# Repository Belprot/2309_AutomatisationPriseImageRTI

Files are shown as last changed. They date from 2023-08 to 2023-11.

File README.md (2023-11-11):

# 2309_AutomatisationPriseImageRTI - Diploma project

## [Projet report](doc/2309_AutomatisationPriseImagesRTI_Rapport_v1_0_0.pdf)

## Project poster
1696541977120-d4f3472b-acff-401a-b088-3b05499086cd_1

## 3D PCB pictures
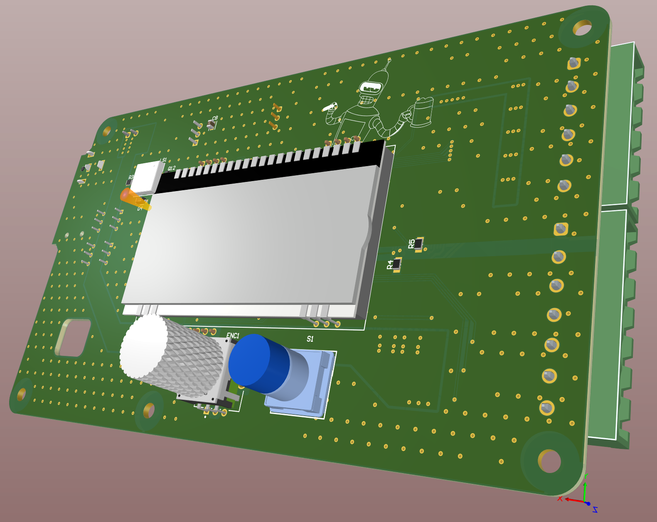
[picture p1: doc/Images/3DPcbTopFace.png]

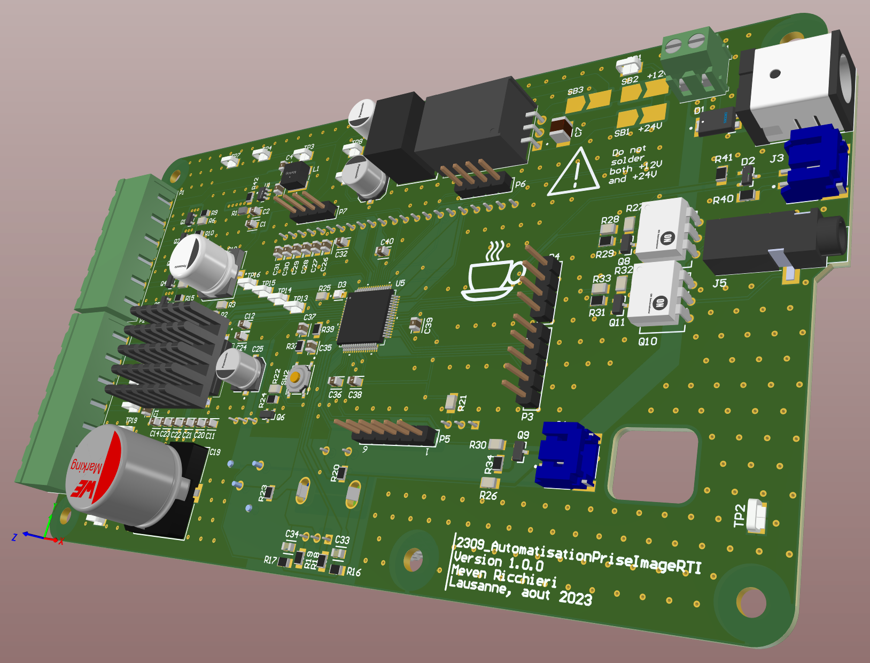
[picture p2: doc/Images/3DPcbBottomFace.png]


## 3D Integration
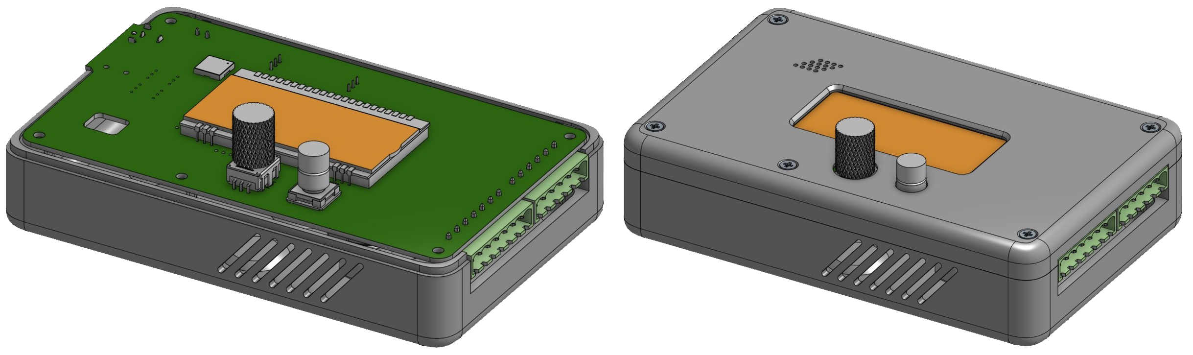
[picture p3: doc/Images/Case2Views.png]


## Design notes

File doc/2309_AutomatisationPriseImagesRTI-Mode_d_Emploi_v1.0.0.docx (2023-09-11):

2309_AutomatisationPriseImagesRTI-Mode_d_Emlpoi_v1.0.0

Mode d’emploi du système :

Le fonctionnement du système est intuitif et facile à maîtriser. Le menu principal propose deux modes d'opération : le mode capture et le mode réglage. Un troisième menu permet de consulter les informations du système sans possibilité d'interaction.

Dans le mode capture, vous pouvez prendre des images de l'objet préalablement placé au centre de la machine. Vous avez le choix entre deux modes de capture : manuel et automatique.

Le mode manuel vous donne un contrôle total sur l'angle du bras motorisé équipé des LEDs de puissance. Vous pouvez également choisir quand déclencher une séquence de prise de 5 images. Dans ce mode, vous avez la possibilité d'indexer la machine pour obtenir l'angle 0 à l'emplacement de l'index. Pour ajuster l'angle du bras, activez la modification de position et tournez l'encodeur. Pour lancer la séquence, appuyez simplement une fois sur le bouton poussoir.

Le mode automatique vous permet de lancer une séquence complète de prise d'images, généralement environ 200 photos de l'objet.

Le menu des réglages vous permet de personnaliser le comportement de la machine pour qu'elle réponde à vos besoins spécifiques. Il est crucial de noter que certaines configurations incorrectes, notamment celles liées au moteur, peuvent rendre le système inutilisable. Une fois que vous avez effectué vos réglages, vous avez la possibilité de sauvegarder la configuration pour qu'elle soit conservée en mémoire et chargée automatiquement au démarrage de la machine.

La Figure ci-dessous présente une vue d'ensemble de tous les menus disponibles.

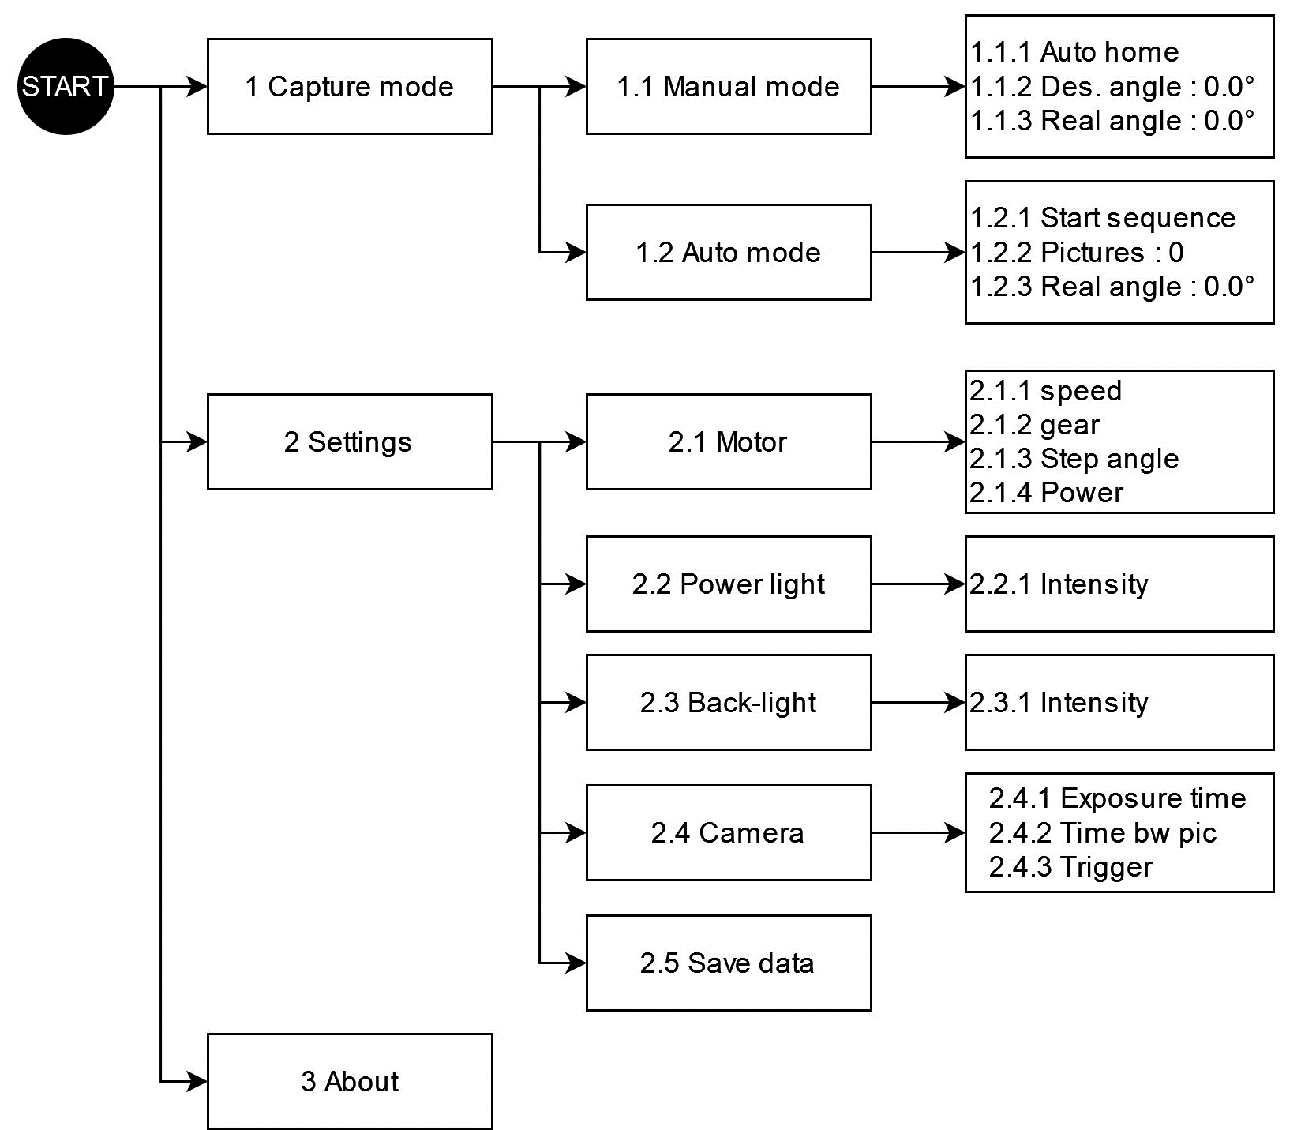
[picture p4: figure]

Figure 1 – Menus

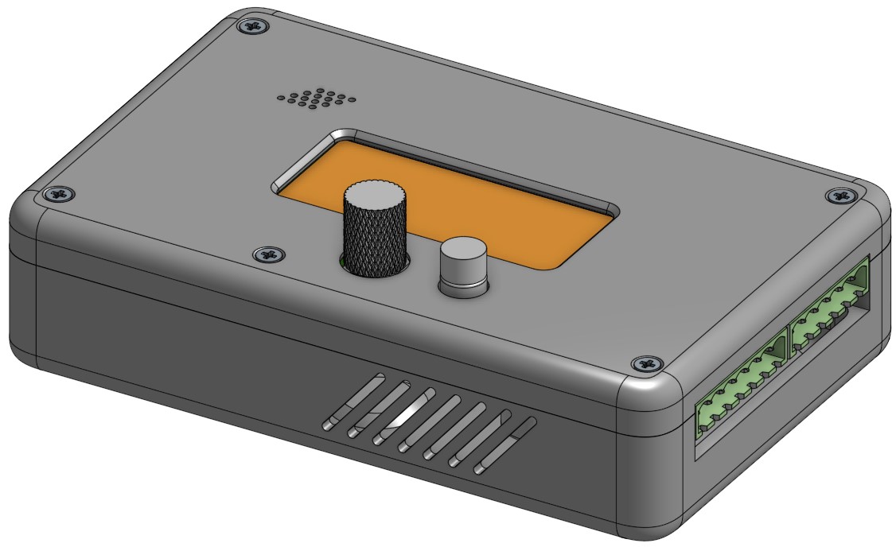
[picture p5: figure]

Connecteur LEDs

Encodeur rotatif

Bouton poussoir

Connecteur moteur

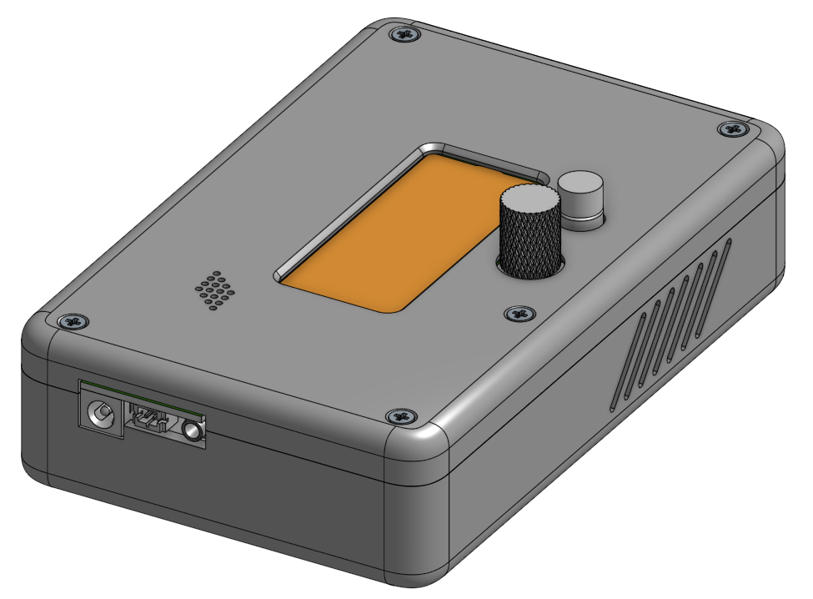
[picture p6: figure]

Connecteur appareil photo

Connecteur contact Reed d’indexage

Connecteur d’alimentation 24V

Meven Ricchieri

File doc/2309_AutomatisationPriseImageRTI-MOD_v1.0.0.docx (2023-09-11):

# Projet ETML-ES – Modification

PROJET: | 2309_AutomatisationPriseImageRTI_v1.0.0
Entreprise/Client: | MCAH / M. Mathieu Bernard-Reymond | Département: | SLO
Demandé par (Prénom, Nom): | M. Serge Castoldi | Date: | 11.09.2023
Objet (No ou réf, pièce, PCB...) | 2309
Version à modifier: | V1

Auteur (ETML-ES): | | Filière: | SLO
Nouvelle version: | | Date:

# 1 Description ou justification

La modifications 1 va permettre d’obtenir un filtre passe bas fonctionnel permettant de limiter le nombre de rebonds du PEC12.

# 2 Référence conception

K:\ES\PROJETS\SLO\2309_AutomatisationPriseImageRTI

# 3 Détail des modifications

# | Description | Fait | Approuvé

1 | Modifier le schéma du filtre du PEC12, R16 doit être connecté directement à la sortie du CHANNEL A et R17 doit être connecté directement à la sortie du CHANNEL B. | NOK
2 | Rechercher l’origine du courant réduit du driver de LED puis effectuer la modification. Piste : Tension d’alimentation trop basse, tester avec alimentation 24V | NOK
3
4
5
6

# 4 Remarques

JMO – Nov 20182309_AutomatisationPriseImageRTI-MOD_v1.0.0.docxPage 1

ECOLE SUPERIEURE ELCO – SLO

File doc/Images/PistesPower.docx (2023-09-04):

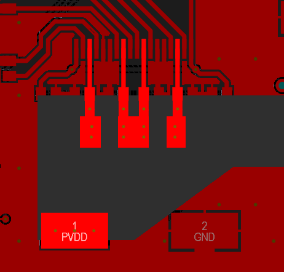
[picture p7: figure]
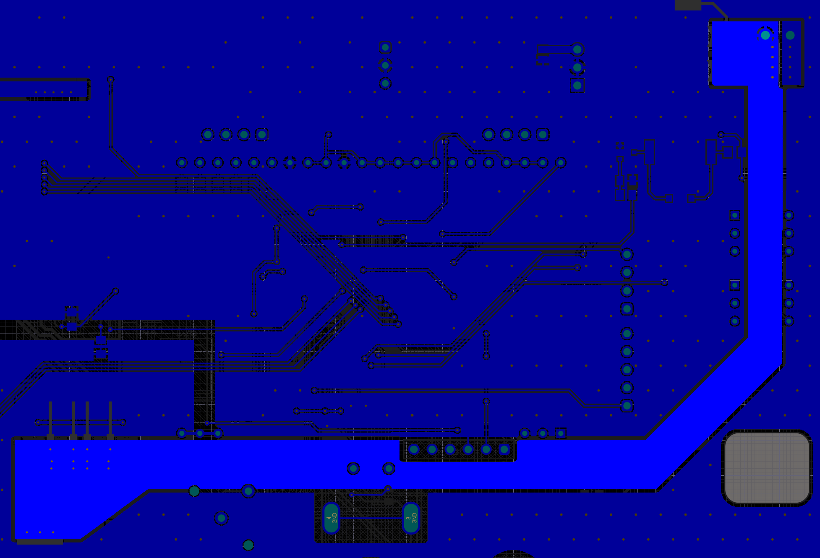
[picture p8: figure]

Entrée d’alimentation du driver en top layer

Driver moteur DRV8432DKD

Entrée de puissance (+24V)

Vue bottom

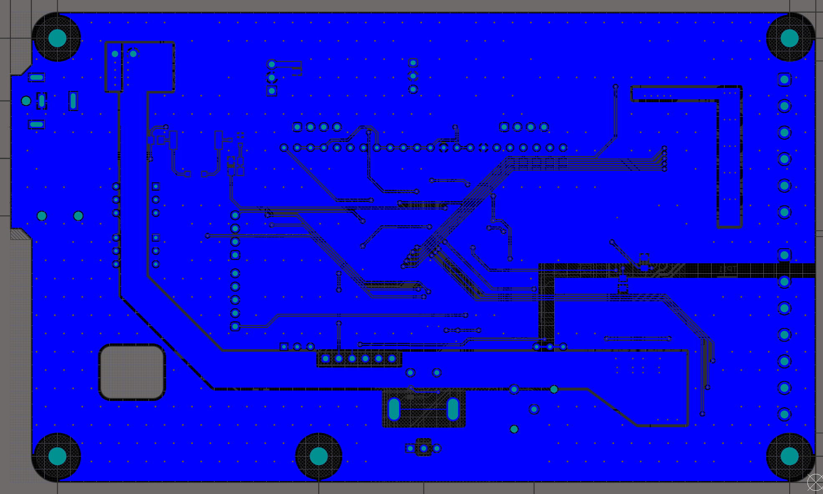
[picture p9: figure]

Retour courant 12V driver LED

Retour courant 24V (moteur)

Retour courant 3.3V

Driver moteur (top layer)

GND

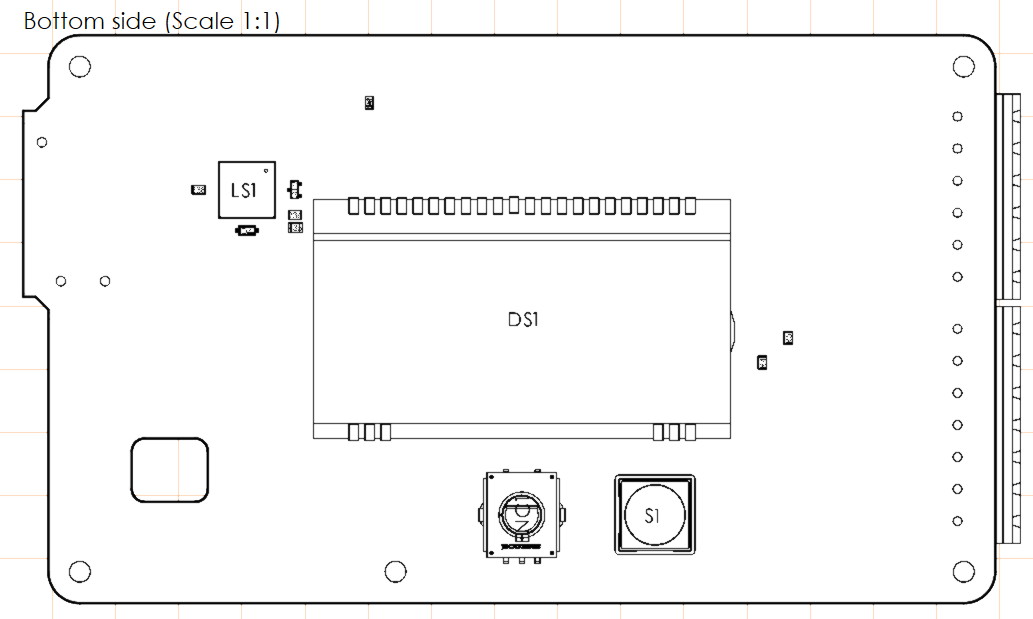
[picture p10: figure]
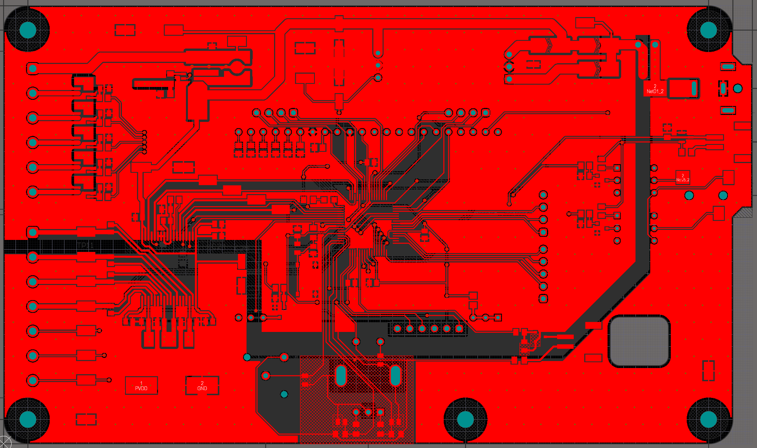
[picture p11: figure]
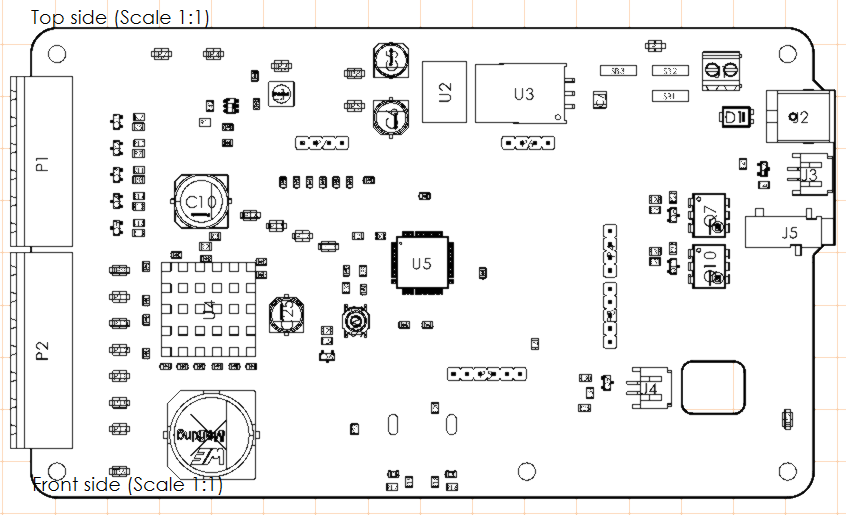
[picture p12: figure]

Connecteur de programmation

Optocoupleurs

MOSFETs de multiplexage

Driver LED

Driver moteur

MCU

Sortie régulateur 12V

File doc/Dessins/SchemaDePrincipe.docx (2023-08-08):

Electronique de commande

Bras motorisé

LEDs de puissance

Élément à photographier

Armature

Moteur de positionnement

Appareil photo

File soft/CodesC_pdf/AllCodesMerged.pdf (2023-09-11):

1 /*******************************************************************************

### 2 MPLAB Harmony Application Source File

3

### 4 Company:

5 Microchip Technology Inc.
6

### 7 File Name: 8 app.c

9

### 10 Summary:

11 This file contains the source code for the MPLAB Harmony application. 12

### 13 Description: 14 This file contains the source code for the MPLAB Harmony application. It 15 implements the logic of the application's state machine and it may call

16 API routines of other MPLAB Harmony modules in the system, such as drivers,

17 system services, and middleware. However, it does not call any of the 18 system interfaces (such as the "Initialize" and "Tasks" functions) of any of 19 the modules in the system or make any assumptions about when those functions 20 are called. That is the responsibility of the configuration-specific system

21 files.
22 *******************************************************************************/ 23
24 // DOM-IGNORE-BEGIN
25 /******************************************************************************* 26 Copyright (c) 2013-2014 released Microchip Technology Inc. All rights reserved. 27

### 28 Microchip licenses to you the right to use, modify, copy and distribute 29 Software only when embedded on a Microchip microcontroller or digital signal 30 controller that is integrated into your product or third party product

31 (pursuant to the sublicense terms in the accompanying license agreement). 32

### 33 You should refer to the license agreement accompanying this Software for

34 additional information regarding your rights and obligations.
35
36 SOFTWARE AND DOCUMENTATION ARE PROVIDED "AS IS" WITHOUT WARRANTY OF ANY KIND,

### 37 EITHER EXPRESS OR IMPLIED, INCLUDING WITHOUT LIMITATION, ANY WARRANTY OF

38 MERCHANTABILITY, TITLE, NON-INFRINGEMENT AND FITNESS FOR A PARTICULAR PURPOSE.

39 IN NO EVENT SHALL MICROCHIP OR ITS LICENSORS BE LIABLE OR OBLIGATED UNDER 40 CONTRACT, NEGLIGENCE, STRICT LIABILITY, CONTRIBUTION, BREACH OF WARRANTY, OR 41 OTHER LEGAL EQUITABLE THEORY ANY DIRECT OR INDIRECT DAMAGES OR EXPENSES 42 INCLUDING BUT NOT LIMITED TO ANY INCIDENTAL, SPECIAL, INDIRECT, PUNITIVE OR 43 CONSEQUENTIAL DAMAGES, LOST PROFITS OR LOST DATA, COST OF PROCUREMENT OF 44 SUBSTITUTE GOODS, TECHNOLOGY, SERVICES, OR ANY CLAIMS BY THIRD PARTIES

45 (INCLUDING BUT NOT LIMITED TO ANY DEFENSE THEREOF), OR OTHER SIMILAR COSTS.
46 *******************************************************************************/ 47 // DOM-IGNORE-END
48
49
50 // ***************************************************************************** 51 // ***************************************************************************** 52 // Section: Included Files
53 // ***************************************************************************** 54 // ***************************************************************************** 55
56 #include "app.h"
57 #include "Mc32_spi_sm.h"
58 #include "lcd_spi.h"
59 #include "system/devcon/src/sys_devcon_local.h" 60 #include "pec12.h"
61 #include "menu.h"
62
63
64
65 // ***************************************************************************** 66 // ***************************************************************************** 67 // Section: Global Data Definitions
68 // ***************************************************************************** 69 // *****************************************************************************

70
71 // ***************************************************************************** 72 /* Application Data
73

### 74 Summary: 75 Holds application data

76

### 77 Description:

78 This structure holds the application's data.
79

### 80 Remarks:

81 This structure should be initialized by the APP_Initialize function. 82
83 Application strings and buffers are be defined outside this structure. 84 */
85
86 APP_DATA appData;
87 SW S1;
88
89 // ***************************************************************************** 90 // ***************************************************************************** 91 // Section: Application Callback Functions
92 // ***************************************************************************** 93 // ***************************************************************************** 94
95 /* TODO: Add any necessary callback functions.
96 */
97
98 // ***************************************************************************** 99 // ***************************************************************************** 100 // Section: Application Local Functions
101 // ***************************************************************************** 102 // ***************************************************************************** 103
104
105 /* TODO: Add any necessary local functions.
106 */
107
108
109 // ***************************************************************************** 110 // ***************************************************************************** 111 // Section: Application Initialization and State Machine Functions
112 // ***************************************************************************** 113 // ***************************************************************************** 114
115
116 //----------------------------------------------------------------------------// APP_UpdateAppState
117 void APP_UpdateAppState(APP_STATES newState){
118
119 appData.appState = newState;
120 }
121
122 //----------------------------------------------------------------------------// APP_Initialize
123 void APP_Initialize ( void )
124 {
125 SPI_Init();
126 /* Place the App state machine in its initial state. */ 127 appData.appState = APP_STATE_INIT;
128 appData.msCounter = 0;
129 appData.backLightIntensitiy = 2500; /* 100% */
130 appData.lightIntensity = 2500; /* 100% */ 131 appData.exposureDuration = 100;
132 appData.timeBetweenPictures = 1000;
133 appData.isFiveShotsSeqEnable = false; 134 appData.seqClock1_ms = 0;
135 appData.angleBwEachSeq = 10;
136 appData.nbrOfShotsPerformed = 0;

137 appData.buzzerIntensity = 2500; 138 appData.valSeq = 0;
139
140 initMenuParam();
141 initStepperParam();
142 }
143
144
145
146 //----------------------------------------------------------------------------// APP_Tasks
147 void APP_Tasks ( void ){
148
149 static uint16_t counter1 = 0; 150 static uint16_t counter2 = 0; 151
152 /* Main state machine */
153 switch(appData.appState){
154 //--------------------------------------------------------------------// APP_STATE_INIT
155 case APP_STATE_INIT:
156 /* Read data from EEPROM to restore presets */
157 readDataFromEeprom(getMyStepperStruct());
158 /* Initialization of the motor */
159 initStepperMotor();
160 /* Update MCPWM Duty-cycle of other PWM with EEPROM data */ 161 updateMcpwmDuty();
162 /* Turn on MCPWM */
163 PLIB_MCPWM_Enable(MCPWM_ID_0);
164 /* Initialization sequence */ 165 initLcd();
166 /* Print initialization menu */ 167 printLcdInit();
168 /* Start useful Timers */
169 DRV_TMR1_Start();
170 DRV_TMR2_Start();
171 /* Print main menu once all peripherals are configured */ 172 printMainMenu();
173 /* States machines update */
174 APP_UpdateAppState(APP_STATE_WAIT);
175 break;
176
177 //--------------------------------------------------------------------// APP_STATE_SERVICE_TASKS
178 /* Frequency = 10'000Hz */
179 case APP_STATE_SERVICE_TASKS:
180
181 /* Process who is responsible of the sequence, motor orders and 182 * lights orders. */
183
184 | // | SIGN_LED_CMDToggle();
185 sequenceManagementProcess(); 186
187 if(counter2 >= 10){
188 /* Frequency = 1'000Hz */
189 counter2 = 0;
190 /* Scan the activity of the rotary encoder */ 191 scanPec12();
192 /* Scan the activity of the switch S1 */ 193 scanSwitch();
194 }
195 if(counter1 >= 1000){
196 /* Frequency = 10Hz */ 197 counter1 = 0;
198 menuManagementProcess(); 199 }
200 counter1++;
201 counter2++;
202

203
204 // Calls the SPI do task state machine 205 SPI_DoTasks();
206
207 /* States machines update */
208 APP_UpdateAppState(APP_STATE_WAIT);
209 break;
210 //--------------------------------------------------------------------// APP_STATE_WAIT
211 case APP_STATE_WAIT:
212 /* Nothing is supposed to happen here */
213 break;
214
215 //--------------------------------------------------------------------// default 216 default:
217 break;
218 }
219 }
220
221
222 //----------------------------------------------------------------------------// APP_Delay_ms
223 void APP_Delay_ms(uint32_t ms){
224
225 DRV_TMR3_Start();
226 | // | SIGN_LED_CMDToggle();
227 while(appData.msCounter < ms){ 228
229 }
230 | // | SIGN_LED_CMDToggle();
231
232 DRV_TMR3_Stop();
233 appData.msCounter = 0;
234 }
235
236 //----------------------------------------------------------------------------// setBlIntensity
237 void setBlIntensity(int32_t *backLightIntensitiy){
238
239 // Limit values to avoid problems
240 if(*backLightIntensitiy < BACKLIGHT_INTENSITY_MIN) *backLightIntensitiy 241 = BACKLIGHT_INTENSITY_MIN;
242 if(*backLightIntensitiy > BACKLIGHT_INTENSITY_MAX) *backLightIntensitiy 243 = BACKLIGHT_INTENSITY_MAX;
244
245 /* 25 = 2500 / 100 */
246 appData.backLightIntensitiy = *backLightIntensitiy * 25; 247 PLIB_MCPWM_ChannelPrimaryDutyCycleSet(MCPWM_ID_0, PWM_BL_CH, 248 appData.backLightIntensitiy);
249 }
250 int32_t getBlIntensity(void){
251
252 return appData.backLightIntensitiy / 25; 253 }
254
255
256 //----------------------------------------------------------------------------// scanSwitch
257 void scanSwitch(void){
258
259 // Save old states for debounce 260 S1.state[3] = S1.state[2]; 261 S1.state[2] = S1.state[1]; 262 S1.state[1] = S1.state[0]; 263 S1.state[0] = SWITCHStateGet();
264
265 // Check if switch is pressed
266 if(S1.state[0] == 1 && S1.state[1] == 1
267 && S1.state[2] == 0 && S1.state[3] == 0){

268
269 S1.isPressed = true;
270 }
271 }
272 //----------------------------------------------------------------------------// getSwitchEvent
273 bool getSwitchEvent(void){
274
275 bool isPressed = S1.isPressed; 276 S1.isPressed = 0;
277
278 return isPressed;
279 }
280
281 //----------------------------------------------------------------------------// initLcdSeq
282 void initLcd(void){
283
284 RESET_LCD_CMDOff();
285 APP_Delay_ms(1);
286 RESET_LCD_CMDOn();
287 APP_Delay_ms(10);
288 initDispl();
289 /* Create degree symbol for LCD uses */ 290 CreateLcdDegreeSymbol(0x01);
291 }
292
293 void updateMcpwmDuty(void){
294
295 /* Update PWMs DutyCycle with data from EEPROM */
296 PLIB_MCPWM_ChannelPrimaryDutyCycleSet(MCPWM_ID_0, PWM_BL_CH, 297 appData.backLightIntensitiy);
298 PLIB_MCPWM_ChannelPrimaryDutyCycleSet(MCPWM_ID_0, PWM_BUZZER_CH, 299 appData.buzzerIntensity);
300 PLIB_MCPWM_ChannelPrimaryDutyCycleSet(MCPWM_ID_0, PWM_DIM_CH, 301 appData.lightIntensity);
302 }
303
304
305
306
307
308 /******************************************************************************* 309 End of File
310 */
311

1 /******************************************************************************* 2 MPLAB Harmony Application Header File
3
4 Company:
5 Microchip Technology Inc.
6
7 File Name:
8 app.h
9
10 Summary:
11 This header file provides prototypes and definitions for the application. 12
13 Description:
14 This header file provides function prototypes and data type definitions for 15 the application. Some of these are required by the system (such as the 16 "APP_Initialize" and "APP_Tasks" prototypes) and some of them are only used 17 internally by the application (such as the "APP_STATES" definition). Both 18 are defined here for convenience.
19 *******************************************************************************/ 20
21 //DOM-IGNORE-BEGIN
22 /******************************************************************************* 23 Copyright (c) 2013-2014 released Microchip Technology Inc. All rights reserved. 24
25 Microchip licenses to you the right to use, modify, copy and distribute
26 Software only when embedded on a Microchip microcontroller or digital signal 27 controller that is integrated into your product or third party product
28 (pursuant to the sublicense terms in the accompanying license agreement). 29
30 You should refer to the license agreement accompanying this Software for
31 additional information regarding your rights and obligations.
32
33 SOFTWARE AND DOCUMENTATION ARE PROVIDED "AS IS" WITHOUT WARRANTY OF ANY KIND, 34 EITHER EXPRESS OR IMPLIED, INCLUDING WITHOUT LIMITATION, ANY WARRANTY OF
35 MERCHANTABILITY, TITLE, NON-INFRINGEMENT AND FITNESS FOR A PARTICULAR PURPOSE. 36 IN NO EVENT SHALL MICROCHIP OR ITS LICENSORS BE LIABLE OR OBLIGATED UNDER
37 CONTRACT, NEGLIGENCE, STRICT LIABILITY, CONTRIBUTION, BREACH OF WARRANTY, OR 38 OTHER LEGAL EQUITABLE THEORY ANY DIRECT OR INDIRECT DAMAGES OR EXPENSES
39 INCLUDING BUT NOT LIMITED TO ANY INCIDENTAL, SPECIAL, INDIRECT, PUNITIVE OR 40 CONSEQUENTIAL DAMAGES, LOST PROFITS OR LOST DATA, COST OF PROCUREMENT OF
41 SUBSTITUTE GOODS, TECHNOLOGY, SERVICES, OR ANY CLAIMS BY THIRD PARTIES
42 (INCLUDING BUT NOT LIMITED TO ANY DEFENSE THEREOF), OR OTHER SIMILAR COSTS.
43 *******************************************************************************/ 44 //DOM-IGNORE-END
45
46 #ifndef _APP_H
47 #define _APP_H
48
49 // ***************************************************************************** 50 // ***************************************************************************** 51 // Section: Included Files
52 // ***************************************************************************** 53 // ***************************************************************************** 54
55 #include "stepperDriver.h"
56 #include "lights.h"
57 #include <stdint.h>
58 #include <stdbool.h>
59 #include <stddef.h>
60 #include <stdlib.h>
61 #include <stdio.h>
62 #include "system_config.h"
63 #include "system_definitions.h"
64
65 // DOM-IGNORE-BEGIN
66 #ifdef __cplusplus // Provide C++ Compatibility 67
68 extern "C" {
69

70 #endif
71 // DOM-IGNORE-END
72
73 // ***************************************************************************** 74 // ***************************************************************************** 75 // Section: Type Definitions
76 // ***************************************************************************** 77 // ***************************************************************************** 78
79 #define SYS_CLK 40000000
80
81 #define PWM_A_CMD_CH MCPWM_CHANNEL1 82 #define PWM_B_CMD_CH MCPWM_CHANNEL1 83 #define PWM_C_CMD_CH MCPWM_CHANNEL2 84 #define PWM_D_CMD_CH MCPWM_CHANNEL2 85 #define PWM_BL_CH MCPWM_CHANNEL3 86 #define PWM_BUZZER_CH MCPWM_CHANNEL4 87 #define PWM_DIM_CH MCPWM_CHANNEL6 88
89 #define MARGIN_LED_DELAY 50
90
91 /* Intensity in percent */
92 #define BACKLIGHT_INTENSITY_MIN 0 93 #define BACKLIGHT_INTENSITY_MAX 100
94
95
96 /* Value used to check if the EEPROM is already writent by this code */
97 #define CONTROL_VALUE 0x11223344
98
99 // ***************************************************************************** 100 /* Application states
101
102 Summary:
103 Application states enumeration
104
105 Description:
106 This enumeration defines the valid application states. These states 107 determine the behavior of the application at various times.
108 */
109
110 typedef enum
111 {
112 /* Application's state machine's initial state. */ 113 APP_STATE_INIT=0,
114 APP_STATE_SERVICE_TASKS,
115 APP_STATE_SERVICE_CAPTURE,
116 APP_STATE_WAIT,
117 } APP_STATES;
118
119 typedef enum{
120
121 SYS_STATE_MENU = 0,
122 SYS_STATE_MANUAL,
123 SYS_STATE_AUTO
124 } SYSTEM_STATES;
125
126
127
128 // ***************************************************************************** 129 /* Application Data
130
131 Summary:
132 Holds application data
133
134 Description:
135 This structure holds the application's data.
136
137 Remarks:
138 Application strings and buffers are be defined outside this structure.

139 */
140
141 typedef enum{
142
143 ALL_LED_DISABLE = 0,
144 PWR_LED1,
145 PWR_LED2,
146 PWR_LED3,
147 PWR_LED4,
148 PWR_LED5,
149
150 }LED_ID;
151
152
153 typedef struct
154 {
155 /* The application's current state */ 156 APP_STATES appState;
157 SYSTEM_STATES systemState;
158 LED_ID ledId;
159 uint32_t msCounter;
160
161 /* LED config */
162 uint16_t lightIntensity; 163 uint16_t timeBetweenPictures; 164 uint16_t exposureDuration; 165
166 /* Auto mode param */
167 uint8_t angleBwEachSeq; 168
169 uint32_t seqClock1_ms; 170 uint32_t seqClock2_ms; 171 bool isFiveShotsSeqEnable; 172 bool isFullImaginSeqEnable; 173 bool isFirstPass;
174 uint16_t nbrOfShotsPerformed; 175 uint8_t valSeq;
176
177 uint16_t backLightIntensitiy; 178
179 uint16_t buzzerIntensity; 180
181 } APP_DATA;
182
183 typedef struct
184 {
185 bool state[4];
186 bool isPressed;
187
188 } SW;
189
190 typedef struct{
191
192 /* Motor data */
193 | int16_t | stepPerSec;
194 | uint16_t | stepPerTurn;
195 | uint16_t | gearValue;
196 | float | anglePerStep;
197
198 /* LEDs data */
199 uint16_t lightIntensity; 200 uint16_t timeBetweenPictures; 201 uint16_t exposureDuration; 202
203 uint16_t backLightIntensitiy; 204
205 /* Security value */
206 uint32_t controlValue;
207

208 } DATA_IN_EEPROM;
209 // ***************************************************************************** 210 // ***************************************************************************** 211 // Section: Application Callback Routines
212 // ***************************************************************************** 213 // ***************************************************************************** 214 /* These routines are called by drivers when certain events occur.
215 */
216
217 // ***************************************************************************** 218 // ***************************************************************************** 219 // Section: Application Initialization and State Machine Functions
220 // ***************************************************************************** 221 // ***************************************************************************** 222
223 /******************************************************************************* 224 Function:
225 void APP_Initialize ( void )
226
227 Summary:
228 MPLAB Harmony application initialization routine.
229
230 Description:
231 This function initializes the Harmony application. It places the 232 application in its initial state and prepares it to run so that its 233 APP_Tasks function can be called.
234
235 Precondition:
236 All other system initialization routines should be called before calling 237 this routine (in "SYS_Initialize").
238
239 Parameters:
240 None.
241
242 Returns:
243 None.
244
245 Example:
246 <code>
247 APP_Initialize();
248 </code>
249
250 Remarks:
251 This routine must be called from the SYS_Initialize function. 252 */
253
254 void APP_Initialize ( void );
255
256
257 /******************************************************************************* 258 Function:
259 void APP_Tasks ( void )
260
261 Summary:
262 MPLAB Harmony Demo application tasks function
263
264 Description:
265 This routine is the Harmony Demo application's tasks function. It 266 defines the application's state machine and core logic.
267
268 Precondition:
269 The system and application initialization ("SYS_Initialize") should be 270 called before calling this.
271
272 Parameters:
273 None.
274
275 Returns:
276 None.

277
278 Example:
279 <code>
280 APP_Tasks();
281 </code>
282
283 Remarks:
284 This routine must be called from SYS_Tasks() routine. 285 */
286
287 void APP_Tasks( void );
288 void APP_Delay_ms(uint32_t ms);
289
290 void setBlIntensity(int32_t *backLightIntensitiy); 291 int32_t getBlIntensity(void);
292
293
294 void scanSwitch(void);
295 bool getSwitchEvent(void); 296
297 void initLcd(void);
298
299 void updateMcpwmDuty(void); 300
301
302
303 #endif /* _APP_H */
304
305 //DOM-IGNORE-BEGIN
306 #ifdef __cplusplus
307 }
308 #endif
309 //DOM-IGNORE-END
310
311 /******************************************************************************* 312 End of File
313 */
314
315

1 /*
2 | * File: | stepperDriver.c
3 * Author: ricch
4 *
5 * Created on August 30, 2023, 10:39 PM 6 *
7 * DRV8432 driver 2H bridge
8 */
9
10
11 #include <stepperDriver.h>
12
13 static STEPPER_DATA stepperData; 14 extern APP_DATA appData;
15
16
17 //----------------------------------------------------------------------------// initStepperData

### 18 void initStepperParam(void){

19
20 | stepperData.isAtHomeInCW | = false;
21 | stepperData.isAtHomeInCCW | = false;
22 | stepperData.isIndexed | = false;
23 stepperData.isInAutoHomeSeq = false; 24
25 | stepperData.performedSteps | = 0;
26 | stepperData.stepToReach | = 0;
27
28 | stepperData.stepPerSec | = 1000;
29
30 | stepperData.stepPerTurn | = 200;
31 | stepperData.gearValue | = 200;
32
33 | stepperData.anglePerStep | = 1.8;
34
35 stepperData.dutyCycleStepper = 30; 36 }
37

### 38 void initStepperMotor(){

39
40 //setStepperPower(&stepperData, &stepperData.dutyCycleStepper); 41
42 /* Disable RESET on both H bridge */
43 RESET_AB_CMDOn();
44 RESET_CD_CMDOn();
45 }
46
47 //----------------------------------------------------------------------------// turnOffStepperPwms
48 /* Disable all PWMs for motor control */

### 49 void turnOffStepperPwms(void){

50
51 /* A */
52 PLIB_MCPWM_ChannelPWMxHEnable (MCPWM_ID_0 ,MCPWM_CHANNEL1); 53 /* B */
54 PLIB_MCPWM_ChannelPWMxHEnable (MCPWM_ID_0 ,MCPWM_CHANNEL2); 55 /* A_ */
56 PLIB_MCPWM_ChannelPWMxLEnable (MCPWM_ID_0 ,MCPWM_CHANNEL1); 57 /* B_ */
58 PLIB_MCPWM_ChannelPWMxLEnable (MCPWM_ID_0 ,MCPWM_CHANNEL2);
59 }
60
61 //----------------------------------------------------------------------------// changeSpeed

### 62 void changeSpeed(STEPPER_DATA *pStepperData){

63
64 uint16_t tmrPerdiod = 0;
65 uint16_t frequency = 0;
66 //uint16_t presc = 0;

67
68 frequency = pStepperData->stepPerSec;
69 //presc = TMR_PrescaleGet_Default(TMR_ID_3); 70 tmrPerdiod = SYS_CLK / (frequency * 16) - 1; 71 PLIB_TMR_Counter16BitClear(TMR_ID_3);
72 PLIB_TMR_Period16BitSet(TMR_ID_3, tmrPerdiod);
73 }
74
75 //----------------------------------------------------------------------------// processStepper

### 76 void processStepper(STEPPER_DATA *pStepperData){

77
78 static uint8_t step = 0;
79 //---------------------------// Counter clockwise CCW

### 80 if(pStepperData->performedSteps > pStepperData->stepToReach){ 81 if(pStepperData->isAtHomeInCCW == false){ 82 switch(step){

83 /* Sequence of 4 steps for CCW rotation */

### 84 case 1:

85 /* A */
86 PLIB_MCPWM_ChannelPWMxHEnable (MCPWM_ID_0 ,MCPWM_CHANNEL1); 87 /* B */
88 PLIB_MCPWM_ChannelPWMxHDisable(MCPWM_ID_0 ,MCPWM_CHANNEL2); 89 /* A_ */
90 PLIB_MCPWM_ChannelPWMxLDisable(MCPWM_ID_0 ,MCPWM_CHANNEL1); 91 /* B_ */
92 PLIB_MCPWM_ChannelPWMxLEnable (MCPWM_ID_0 ,MCPWM_CHANNEL2); 93 break;
94

### 95 case 2:

96 PLIB_MCPWM_ChannelPWMxHEnable (MCPWM_ID_0 ,MCPWM_CHANNEL1); 97 PLIB_MCPWM_ChannelPWMxHEnable (MCPWM_ID_0 ,MCPWM_CHANNEL2); 98 PLIB_MCPWM_ChannelPWMxLDisable(MCPWM_ID_0 ,MCPWM_CHANNEL1); 99 PLIB_MCPWM_ChannelPWMxLDisable(MCPWM_ID_0 ,MCPWM_CHANNEL2); 100 break;
101
102 case 3:
103 PLIB_MCPWM_ChannelPWMxHDisable(MCPWM_ID_0 ,MCPWM_CHANNEL1); 104 PLIB_MCPWM_ChannelPWMxHEnable (MCPWM_ID_0 ,MCPWM_CHANNEL2); 105 PLIB_MCPWM_ChannelPWMxLEnable (MCPWM_ID_0 ,MCPWM_CHANNEL1); 106 PLIB_MCPWM_ChannelPWMxLDisable(MCPWM_ID_0 ,MCPWM_CHANNEL2); 107 break;
108
109 case 0:
110 PLIB_MCPWM_ChannelPWMxHDisable(MCPWM_ID_0 ,MCPWM_CHANNEL1); 111 PLIB_MCPWM_ChannelPWMxHDisable(MCPWM_ID_0 ,MCPWM_CHANNEL2); 112 PLIB_MCPWM_ChannelPWMxLEnable (MCPWM_ID_0 ,MCPWM_CHANNEL1); 113 PLIB_MCPWM_ChannelPWMxLEnable (MCPWM_ID_0 ,MCPWM_CHANNEL2); 114 break;
115 }
116 step++;
117 }
118 /* Four steps performed in CCW */ 119 if(step == 4){
120
121 step = 0;
122 pStepperData->performedSteps -= 4;
123 }
124 /* Index is reach in CCW */
125 if(INDEXStateGet() && pStepperData->isAtHomeInCW == false){ 126
127 pStepperData->isAtHomeInCCW = true;
128 | // | pStepperData->stepToDoReach = pStepperData->performedStep;
129
130 if(pStepperData->isInAutoHomeSeq == true){
131
132 pStepperData->stepToReach = 0;
133 pStepperData->performedSteps = 0; 134 pStepperData->isIndexed = true;

135 pStepperData->isInAutoHomeSeq = false; 136 }
137 }
138 else pStepperData->isAtHomeInCCW = false;
139 }
140 //---------------------------// Clockwise CW
141 else if(pStepperData->performedSteps < pStepperData->stepToReach){ 142 if(pStepperData->isAtHomeInCW == false){
143 switch(step){
144 /* Sequence of 4 steps for CW rotation */
145 case 1:
146 /* A */
147 PLIB_MCPWM_ChannelPWMxHEnable (MCPWM_ID_0 ,MCPWM_CHANNEL1); 148 /* B */
149 PLIB_MCPWM_ChannelPWMxHDisable(MCPWM_ID_0 ,MCPWM_CHANNEL2); 150 /* A_ */
151 PLIB_MCPWM_ChannelPWMxLDisable(MCPWM_ID_0 ,MCPWM_CHANNEL1); 152 /* B_ */
153 PLIB_MCPWM_ChannelPWMxLEnable (MCPWM_ID_0 ,MCPWM_CHANNEL2); 154 break;
155
156 case 0:
157 PLIB_MCPWM_ChannelPWMxHEnable (MCPWM_ID_0 ,MCPWM_CHANNEL1); 158 PLIB_MCPWM_ChannelPWMxHEnable (MCPWM_ID_0 ,MCPWM_CHANNEL2); 159 PLIB_MCPWM_ChannelPWMxLDisable(MCPWM_ID_0 ,MCPWM_CHANNEL1); 160 PLIB_MCPWM_ChannelPWMxLDisable(MCPWM_ID_0 ,MCPWM_CHANNEL2); 161 break;
162
163 case 3:
164 PLIB_MCPWM_ChannelPWMxHDisable(MCPWM_ID_0 ,MCPWM_CHANNEL1); 165 PLIB_MCPWM_ChannelPWMxHEnable (MCPWM_ID_0 ,MCPWM_CHANNEL2); 166 PLIB_MCPWM_ChannelPWMxLEnable (MCPWM_ID_0 ,MCPWM_CHANNEL1); 167 PLIB_MCPWM_ChannelPWMxLDisable(MCPWM_ID_0 ,MCPWM_CHANNEL2); 168 break;
169
170 case 2:
171 PLIB_MCPWM_ChannelPWMxHDisable(MCPWM_ID_0 ,MCPWM_CHANNEL1); 172 PLIB_MCPWM_ChannelPWMxHDisable(MCPWM_ID_0 ,MCPWM_CHANNEL2); 173 PLIB_MCPWM_ChannelPWMxLEnable (MCPWM_ID_0 ,MCPWM_CHANNEL1); 174 PLIB_MCPWM_ChannelPWMxLEnable (MCPWM_ID_0 ,MCPWM_CHANNEL2); 175 break;
176 }
177 step++;
178 }
179 /* Four steps performed in CW */ 180 if(step == 4){
181
182 step = 0;
183 pStepperData->performedSteps += 4;
184 }
185 /* Index is reach in CW */
186 if(INDEXStateGet() && pStepperData->isAtHomeInCCW == false){ 187
188 pStepperData->isAtHomeInCW = true;
189 /* Stop the automatic sequence */
190 appData.isFullImaginSeqEnable = false;
191 /* Stop the motor */
192 pStepperData->stepToReach = pStepperData->performedSteps; 193 }
194 else pStepperData->isAtHomeInCW = false;
195 }
196
197
198 // The motor reach its desired position
199 | // | if(pStepperData->performedSteps == pStepperData->stepToReach){
200 | //// | turnOffStepperPwms();
201 | // | } else {
202 //
203 | //// | PLIB_MCPWM_Enable(MCPWM_ID_0);

204 | // | }
205 }
206
207
208
209 //----------------------------------------------------------------------------// setSpeed 210 void setSpeed(STEPPER_DATA *pStepperData, uint32_t *pStepPerSec){
211
212 // Limit values to avoid problems
213 if(*pStepPerSec < STEP_PER_SEC_MIN) *pStepPerSec = STEP_PER_SEC_MIN; 214 if(*pStepPerSec > STEP_PER_SEC_MAX) *pStepPerSec = STEP_PER_SEC_MAX; 215
216 // Save data
217 pStepperData->stepPerSec = *pStepPerSec;
218 }
219
220 int32_t getSpeed(STEPPER_DATA *pStepperData){ 221
222 return pStepperData->stepPerSec;
223 }
224
225 //----------------------------------------------------------------------------// setGearReduction
226 void setGearReduction(STEPPER_DATA *pStepperData, uint32_t *pGearValue){
227
228 // Limit values to avoid problems
229 if(*pGearValue < GEAR_VALUE_MIN) *pGearValue = GEAR_VALUE_MIN;
230 if(*pGearValue > GEAR_VALUE_MAX) *pGearValue = GEAR_VALUE_MAX; 231
232 // Save data
233 pStepperData->gearValue = *pGearValue;
234 }
235 //----------------------------------------------------------------------------// getGearReduction
236 uint32_t getGearReduction(STEPPER_DATA *pStepperData){
237
238 return pStepperData->gearValue;
239 }
240
241 //----------------------------------------------------------------------------// setAnglePerStep
242 void setAnglePerStep(STEPPER_DATA *pStepperData, uint32_t *pAnglePerStep){
243
244 float temp = (*pAnglePerStep / 10.0);
245
246 // Limit values to avoid problems
247 if(temp < ANGLE_PER_STEP_MIN) temp = (ANGLE_PER_STEP_MIN); 248 if(temp > ANGLE_PER_STEP_MAX) temp = (ANGLE_PER_STEP_MAX); 249 *pAnglePerStep = temp * 10;
250
251 // Save data
252 pStepperData->anglePerStep = temp;
253 }
254 //----------------------------------------------------------------------------// getAnglePerStep
255 uint32_t getAnglePerStep(STEPPER_DATA *pStepperData){
256
257 // x10 ???
258 return pStepperData->anglePerStep * 10;
259 }
260
261 //----------------------------------------------------------------------------// getPerformedSteps
262 int32_t getPerformedSteps(STEPPER_DATA *pStepperData){
263
264 return pStepperData->performedSteps / pStepperData->stepPerTurn; 265 }
266
267

268 //----------------------------------------------------------------------------// setRotationToDo
269 void setRotationToDo(STEPPER_DATA *pStepperData, int32_t *pRotationToDo){
270
271 // Limit values to avoid problems
272 if(*pRotationToDo < ROTATION_TO_DO_MIN) *pRotationToDo = ROTATION_TO_DO_MIN; 273 if(*pRotationToDo > ROTATION_TO_DO_MAX) *pRotationToDo = ROTATION_TO_DO_MAX; 274
275 // Save data
276 pStepperData->stepToReach = *pRotationToDo * pStepperData->stepPerTurn; 277 }
278 //----------------------------------------------------------------------------// getRotationTodo
279 int32_t getRotationToDo(STEPPER_DATA *pStepperData){
280
281 return pStepperData->stepToReach / pStepperData->stepPerTurn;
282 }
283
284 //----------------------------------------------------------------------------// autoHome 285 void startAutoHome(STEPPER_DATA *pStepperData){
286
287 pStepperData->isInAutoHomeSeq = true;
288 // Check if the arm is not at home
289 if(pStepperData->isAtHomeInCCW == false){
290 // Put steps to do for returning home in CCW
291 pStepperData->stepToReach = -50000; // DEFINE? STEP_TO_DO_MAX 292 }
293 }
294
295 //----------------------------------------------------------------------------// setStepperPower
296 void setStepperPower(STEPPER_DATA *pStepperData, uint16_t *pDutyCycleStepper){ 297
298 uint16_t dutyValCh1 = 0;
299
300 // Limit values to avoid problems
301 if(*pDutyCycleStepper < MCPWM_DUTYCYCLE_MIN) *pDutyCycleStepper 302 = MCPWM_DUTYCYCLE_MIN;
303 if(*pDutyCycleStepper > MCPWM_DUTYCYCLE_MAX) *pDutyCycleStepper 304 = MCPWM_DUTYCYCLE_MAX;
305
306 /* Save configuration in the structure */
307 pStepperData->dutyCycleStepper = *pDutyCycleStepper; 308
309 /* Must be the inverse of the CHANNEL 1 */
310 dutyValCh1 = MCPWM_PRIMARY_PERIOD - *pDutyCycleStepper;
311
312 PLIB_MCPWM_ChannelPrimaryDutyCycleSet(MCPWM_ID_0 ,MCPWM_CHANNEL1, 313 dutyValCh1);
314 PLIB_MCPWM_ChannelPrimaryDutyCycleSet(MCPWM_ID_0 ,MCPWM_CHANNEL2, 315 *pDutyCycleStepper);
316 }
317
318 int16_t getStepperPower(STEPPER_DATA *pStepperData){ 319
320 return pStepperData->dutyCycleStepper;
321 }
322
323
324 //----------------------------------------------------------------------------// getStepperStruct
325 STEPPER_DATA* getMyStepperStruct(void){
326
327 /* Return the address of the structure */ 328 return &stepperData;
329 }

1 /*
2 | * File: | stepperDriver.h
3 * Author: ricch
4 *
5 * Created on August 30, 2023, 10:39 PM 6 */
7
8 #ifndef STEPPERDRIVER_H
9 #define STEPPERDRIVER_H
10
11 #ifdef __cplusplus

### 12 extern "C" {

13 #endif
14
15 #include <stdint.h>
16 #include "system_definitions.h" 17
18 // Defines
19 #define STEP_PER_SEC_MIN 40 20 #define STEP_PER_SEC_MAX 1000 21
22 #define GEAR_VALUE_MIN 1
23 #define GEAR_VALUE_MAX 1000 24
25 #define STEP_PER_TURN_MIN 4 26 #define STEP_PER_TURN_MAX 400 27
28 #define ANGLE_PER_STEP_MIN 0.1 29 #define ANGLE_PER_STEP_MAX 10.0 30
31 #define ROTATION_TO_DO_MIN -50000 32 #define ROTATION_TO_DO_MAX 50000 33
34 /* Period for 50kHz PWMs */
35 #define MCPWM_PRIMARY_PERIOD 199 36 #define MCPWM_DUTYCYCLE_MIN 9 37 #define MCPWM_DUTYCYCLE_MAX 189 38
39 // Structures

### 40 typedef struct{

41
42 /* Motion motor data */
43 | bool | isAtHomeInCW;
44 | bool | isAtHomeInCCW;
45 | bool | isIndexed;
46 | bool | isInAutoHomeSeq;
47
48 | int32_t | performedSteps;
49 | int32_t | stepToReach;
50
51 /* Motor characteristics */
52 | int16_t | stepPerSec;
53
54 | uint16_t | stepPerTurn;
55 | uint16_t | gearValue;
56
57 | float | anglePerStep;
58
59 | uint16_t | dutyCycleStepper;
60
61 } STEPPER_DATA;
62
63
64
65 // Prototypes
66 void initStepperParam(void);
67 void turnOffStepperPwms(void);
68 void changeSpeed(STEPPER_DATA *pStepperData); 69 void processStepper(STEPPER_DATA *pStepperData);

70
71
72 void setSpeed(STEPPER_DATA *pStepperData, uint32_t *pStepPerSec);
73 int32_t getSpeed(STEPPER_DATA *pStepperData);
74 void setGearReduction(STEPPER_DATA *pStepperData, uint32_t *pGearValue); 75 uint32_t getGearReduction(STEPPER_DATA *pStepperData);
76 void setAnglePerStep(STEPPER_DATA *pStepperData, uint32_t *pAnglePerStep); 77 uint32_t getAnglePerStep(STEPPER_DATA *pStepperData);
78 int32_t getPerformedSteps(STEPPER_DATA *pStepperData);
79 void setRotationToDo(STEPPER_DATA *pStepperData, int32_t *pRotationToDo); 80 int32_t getRotationToDo(STEPPER_DATA *pStepperData);
81 void startAutoHome(STEPPER_DATA *pStepperData);
82
83 void setStepperPower(STEPPER_DATA *pStepperData, uint16_t *pDutyCycleStepper); 84 int16_t getStepperPower(STEPPER_DATA *pStepperData);
85
86 STEPPER_DATA* getMyStepperStruct(void);
87
88 #ifdef __cplusplus
89 }
90 #endif
91
92 #endif /* STEPPERDRIVER_H */ 93
94

1 /*
2 | * File: | menu.c
3 * Author: ricch
4 *
5 * Created on August 30, 2023, 10:15 AM 6 */
7
8 #include "menu.h"
9 #include "lcd_spi.h"
10 #include "stdio.h"
11 #include "pec12.h"
12 #include "stepperDriver.h" 13
14
15 MENU menu;
16 extern APP_DATA appData;
17 bool isInModifMode = 0;
18 bool isFirstDataProcessPass = false; 19
20

### 21 void initMenuParam(){

22
23 menu.menuPage = 0;
24 menu.menuSize = 2;
25 menu.menuState = MAIN_MENU; 26 }
27
28
29 //____________________________________________________________________________// menuManagementProcess

### 30 void menuManagementProcess(void){

31
32 static int32_t pec12RotationValue = 0;
33
34 /* Get PEC12 increments or decrements if there are */
35 int incrOrDecr = getPec12IncrOrDecr();
36 //------------------------------------------------------------------------// isInModifMode == true

### 37 if(isInModifMode){

38
39 pec12RotationValue += incrOrDecr;
40 menuDataProcess(&pec12RotationValue, getMyStepperStruct()); 41 menuPrintProcess(getMyStepperStruct());
42
43 /* PEC12 switch pressed */

### 44 if(getPec12SwitchEvent()){

45
46 /* Leave modification mode */
47 isInModifMode = false;
48 /* Put the cursor on the first line */ 49 pec12RotationValue = 0;
50 }
51 }
52 //------------------------------------------------------------------------// isInModifMode == false

### 53 else if(isInModifMode == false){

54
55 pec12RotationValue += incrOrDecr;
56

### 57 if(pec12RotationValue > menu.menuSize) pec12RotationValue =

58 menu.menuSize;
59 else if(pec12RotationValue < 0) pec12RotationValue = 0; 60

### 61 if(pec12RotationValue <= 3){

62
63 menu.menuPage = 0;
64 menuPrintProcess(getMyStepperStruct()); 65 printCursor(pec12RotationValue);
66 }

### 67 else{

68
69 menu.menuPage = 1;
70 menuPrintProcess(getMyStepperStruct()); 71 printCursor(pec12RotationValue - 4); 72 }
73
74 /* PEC12 switch pressed */

### 75 if(getPec12SwitchEvent()){

76
77 menuActionProcess(pec12RotationValue);
78 menuDataProcess(&pec12RotationValue, getMyStepperStruct()); 79 menuPrintProcess(getMyStepperStruct());
80
81 /* Put the cursor on the first line */
82 | // | pec12RotationValue = 0;
83 }
84 }

### 85 if(getSwitchEvent()){

86
87 //startFiveShotsSequence();
88 | // | startFullImagingSequence();
89

### 90 switch (menu.menuState){

91

### 92 case MANUAL_MODE_MENU:

93 /* Start a sequence of 5 pictures */ 94 //startFiveShotsSequence();
95 startFiveShotsSeqProcess();
96 break;
97

### 98 default:

99 break;
100 }
101 }
102 }
103
104
105 //____________________________________________________________________________// 106 void menuActionProcess(int32_t pec12RotationValue){
107
108 /* Menu action switch */
109 if(isInModifMode == false){
110 switch(menu.menuState){
111
112 //----------------------------------------------------------------// Main
| | menu
113 case MAIN_MENU:
114
115 switch(pec12RotationValue){
116
117 case CAPTURE_MODE_SEL:
118 menu.menuState = CAPTURE_MODE_MENU; 119 menu.menuSize = 2;
120 break;
121
122 case SETTINGS_SEL:
123 menu.menuState = SETTINGS_MENU; 124 menu.menuSize = 5;
125 break;
126
127 case ABOUT_SEL:
128 menu.menuState = ABOUT_MENU; 129 menu.menuSize = 0;
130 break;
131 }
132 break;
133
134 //----------------------------------------------------------------// Main

menu -> Choice menu
135 case CAPTURE_MODE_MENU:
136
137 switch(pec12RotationValue){
138
139 case RETURN_SEL:
140 menu.menuState = MAIN_MENU; 141 menu.menuSize = 2;
142 break;
143
144 case MANUAL_MODE_SEL:
145 menu.menuState = MANUAL_MODE_MENU; 146 menu.menuSize = 2;
147 break;
148
149 case AUTOMATIC_MODE_SEL:
150 menu.menuState = AUTOMATIC_MODE_MENU; 151 menu.menuSize = 1;
152 break;
153 }
154 break;
155
156 //----------------------------------------------------------------// Main menu -> Choice menu -> Manual Mode 157 case MANUAL_MODE_MENU:
158 switch(pec12RotationValue){
159
160 case RETURN_SEL:
161 menu.menuState = CAPTURE_MODE_MENU; 162 menu.menuSize = 2;
163 break;
164
165 case AUTO_HOME_SEL:
166 menu.menuState = AUTO_HOME_MENU; 167 menu.menuSize = 1;
168 break;
169
170 case ANGLE_SEL:
171 menu.modifState = ANGLE_MODIF; 172 isInModifMode = true;
173 isFirstDataProcessPass = true; 174 break;
175 }
176 break;
177
178 //----------------------------------------------------------------// Main menu -> Auto menu
179 case AUTOMATIC_MODE_MENU:
180 switch(pec12RotationValue){
181
182 case RETURN_SEL:
183 menu.menuState = CAPTURE_MODE_MENU; 184 menu.menuSize = 2;
185 break;
186
187 case AUTOMATIC_MODE_START_SEL:
188 menu.modifState = AUTOMATIC_MODE_START; 189 isInModifMode = true;
190 isFirstDataProcessPass = true;
191 break;
192 }
193 break;
194
195 //----------------------------------------------------------------// Main menu -> Manual menu -> Auto home 196 case AUTO_HOME_MENU:
197 switch(pec12RotationValue){
198
199 case RETURN_SEL:

200 menu.menuState = MANUAL_MODE_MENU; 201 menu.menuSize = 2;
202 break;
203
204 case AUTO_HOME_START_SEL:
205 menu.modifState = AUTO_HOME_START; 206 isInModifMode = true;
207 isFirstDataProcessPass = true; 208 break;
209 }
210 break;
211
212 //returnToHome(); PEUT ETRE METTRE AILLEUR
213 break;
214
215 //----------------------------------------------------------------// Main menu -> Settings menu
216 case SETTINGS_MENU:
217
218 switch(pec12RotationValue){
219
220 case RETURN_SEL:
221 menu.menuState = MAIN_MENU; 222 menu.menuSize = 2;
223 break;
224
225 case MOTOR_SEL:
226 menu.menuState = MOTOR_MENU; 227 menu.menuSize = 4;
228 break;
229
230 case LEDS_SEL:
231 menu.menuState = LIGHT_MENU; 232 menu.menuSize = 1;
233 break;
234
235 case BACKLIGHT_SEL:
236 menu.menuState = BACKLIGHT_MENU; 237 menu.menuSize = 1;
238 break;
239
240 case CAMERA_SEL:
241 menu.menuState = CAMERA_MENU; 242 menu.menuSize = 3;
243 break;
244
245 case SAVE_DATA_SEL:
246 menu.menuState = SAVE_DATA_MENU; 247 menu.menuSize = 1;
248 break;
249
250 }
251 break;
252
253 //----------------------------------------------------------------// Main menu -> Settings menu -> Motor menu 254 case MOTOR_MENU:
255 switch(pec12RotationValue){
256
257 case RETURN_SEL:
258 menu.menuState = SETTINGS_MENU; 259 menu.menuSize = 5;
260 break;
261
262 case SPEED_SEL:
263 menu.modifState = SPEED_MODIF; 264 isInModifMode = true;
265 isFirstDataProcessPass = true; 266 break;

267
268 case GEAR_SEL:
269 menu.modifState = GEAR_MODIF; 270 isInModifMode = true;
271 isFirstDataProcessPass = true; 272 break;
273
274 case STEP_PER_TURN_SEL:
275 menu.modifState = STEP_PER_TURN_MODIF; 276 isInModifMode = true;
277 isFirstDataProcessPass = true; 278 break;
279
280 case POWER_SEL:
281 menu.modifState = POWER_MODIF; 282 isInModifMode = true;
283 isFirstDataProcessPass = true; 284 break;
285 }
286 break;
287
288 //----------------------------------------------------------------// Main menu -> Settings menu -> Light menu 289 case LIGHT_MENU:
290 switch(pec12RotationValue){
291
292 case RETURN_SEL:
293 menu.menuState = SETTINGS_MENU; 294 menu.menuSize = 5;
295 break;
296
297 case LIGHT_INTENSITY_SEL:
298 menu.modifState = LIGHT_INTENSITY_MODIF; 299 isInModifMode = true;
300 isFirstDataProcessPass = true;
301 break;
302
303 | // | case LIGHT_TIME_SEL: // <--- in camera param
304 | // | menu.modifState = LIGHT_TIME_MODIF;
305 | // | isInModifMode = true;
306 | // | isFirstDataProcessPass = true;
307 | // | break;
308 }
309 break;
310
311 //----------------------------------------------------------------// Main
| | menu -> Settings menu -> Back-light menu
312 case BACKLIGHT_MENU:
313 switch(pec12RotationValue){
314
315 case RETURN_SEL:
316 menu.menuState = SETTINGS_MENU; 317 menu.menuSize = 5;
318 break;
319
320 case LIGHT_INTENSITY_SEL:
321 menu.modifState = BL_INTENSITY_MODIF; 322 isInModifMode = true;
323 isFirstDataProcessPass = true; 324 break;
325 }
326 break;
327
328 //----------------------------------------------------------------// Main
| | menu -> Settings menu -> Camera
329 case CAMERA_MENU:
330 switch(pec12RotationValue){
331
332 case RETURN_SEL:

333 menu.menuState = SETTINGS_MENU; 334 menu.menuSize = 5;
335 break;
336
337 case EXPOSURE_TIME_SEL:
338 menu.modifState = EXPOSURE_TIME_MODIF; 339 isInModifMode = true;
340 break;
341
342 case TIME_BW_PICTURES_SEL:
343 menu.modifState = TIME_BW_PICTURES_MODIF; 344 isInModifMode = true;
345 break;
346 }
347 isFirstDataProcessPass = true;
348 break;
349
350 //----------------------------------------------------------------// Main menu -> Settings menu -> Save data 351 case SAVE_DATA_MENU:
352 switch(pec12RotationValue){
353
354 case RETURN_SEL:
355 menu.menuState = SETTINGS_MENU; 356 menu.menuSize = 5;
357 break;
358
359 case SAVE_DATA_SEL - 4:
360 menu.modifState = SAVE_DATA_START; 361 isInModifMode = true;
362 break;
363 }
364 isFirstDataProcessPass = true;
365 break;
366
367 //----------------------------------------------------------------// Main menu -> About menu
368 case ABOUT_MENU:
369
370 switch(pec12RotationValue){
371
372 case RETURN_SEL:
373 menu.menuState = MAIN_MENU; 374 menu.menuSize = 2;
375 break;
376 }
377 break;
378
379 default:
380 break;
381 }
382 }
383 }
384
385 //____________________________________________________________________________// 386 void menuDataProcess(int32_t *pec12RotationValue, STEPPER_DATA *pStepperData){ 387
388 /* Data action switch */
389 if(isInModifMode){
390 switch(menu.modifState){
391
392 //----------------------------------------------------------------// ANGLE_MODIF
393 case ANGLE_MODIF:
394 if(isFirstDataProcessPass){
395
396 isFirstDataProcessPass = false;
397 /* A TESTER ET VALIDER, PERTE DE PAS POSSIBLE */ 398 *pec12RotationValue = getRotationToDo(pStepperData);

399 }
400 setRotationToDo(pStepperData, pec12RotationValue);
401 break;
402
403 //----------------------------------------------------------------// SPEED_MODIF
404 case SPEED_MODIF:
405 if(isFirstDataProcessPass){
406
407 isFirstDataProcessPass = false;
408 *pec12RotationValue = getSpeed(pStepperData); 409 }
410 setSpeed(pStepperData, pec12RotationValue);
411 break;
412
413 //----------------------------------------------------------------// GEAR_MODIF
414 case GEAR_MODIF:
415 if(isFirstDataProcessPass){
416
417 isFirstDataProcessPass = false;
418 *pec12RotationValue = getGearReduction(pStepperData); 419 }
420 setGearReduction(pStepperData, pec12RotationValue);
421 break;
422
423 //----------------------------------------------------------------// STEP_PER_TURN_MODIF
424 case STEP_PER_TURN_MODIF :
425 if(isFirstDataProcessPass){
426
427 isFirstDataProcessPass = false;
428 *pec12RotationValue = getAnglePerStep(pStepperData); 429 }
430 setAnglePerStep(pStepperData, pec12RotationValue);
431 break;
432
433 //----------------------------------------------------------------// POWER_MODIF
434 case POWER_MODIF:
435 if(isFirstDataProcessPass){
436
437 isFirstDataProcessPass = false;
438 *pec12RotationValue = getStepperPower(pStepperData);
439 }
440 setStepperPower(pStepperData, (uint16_t*)pec12RotationValue); /// ????_____Dwaf-ad-***
441 break;
442
443 //----------------------------------------------------------------// BL_INTENSITY_MODIF
444 case BL_INTENSITY_MODIF :
445 if(isFirstDataProcessPass){
446
447 isFirstDataProcessPass = false; 448 *pec12RotationValue = getBlIntensity(); 449 }
450 setBlIntensity(pec12RotationValue);
451 break;
452
453 //----------------------------------------------------------------// LIGHT_INTENSITY_MODIF
454 case LIGHT_INTENSITY_MODIF:
455 if(isFirstDataProcessPass){
456
457 isFirstDataProcessPass = false;
458 *pec12RotationValue = getLightIntensity(); 459 }
460 setLightIntensity(pec12RotationValue);

461 break;
462
463 //----------------------------------------------------------------// EXPOSURE_TIME_MODIF
464 case EXPOSURE_TIME_MODIF:
465 if(isFirstDataProcessPass){
466
467 isFirstDataProcessPass = false;
468 *pec12RotationValue = getExposureTime(); 469 }
470 setExposureTime(pec12RotationValue);
471 break;
472
473 //----------------------------------------------------------------// TIME_BW_PICTURES_MODIF
474 case TIME_BW_PICTURES_MODIF:
475 if(isFirstDataProcessPass){
476
477 isFirstDataProcessPass = false;
478 *pec12RotationValue = getTimeBwPictures(); 479 }
480 setTimeBwPictures(pec12RotationValue);
481 break;
482
483 //----------------------------------------------------------------// SAVE_DATA_START
484 case SAVE_DATA_START:
485 if(isFirstDataProcessPass){
486
487 isFirstDataProcessPass = false;
488 | // | isInModifMode = false; // AFFICHER .. ECRAN
489 saveDataInEeprom(pStepperData);
490 /* Once the data are saved, back to previous menu */ 491 isInModifMode = false;
492 menu.menuState = SETTINGS_MENU;
493 menu.menuSize = 5;
494 }
495 break;
496
497 //----------------------------------------------------------------//
| | AUTO_HOME_START
498 case AUTO_HOME_START:
499 if(isFirstDataProcessPass){
500
501 isFirstDataProcessPass = false;
502 /* Start the auto home seq. */
503 startAutoHome(pStepperData);
504 /* Once auto home seq. is started, back to previous menu */ 505 isInModifMode = false;
506 menu.menuState = MANUAL_MODE_MENU;
507 menu.menuSize = 2;
508 }
509 break;
510
511 //----------------------------------------------------------------//
| | AUTOMATIC_MODE_START
512 case AUTOMATIC_MODE_START:
513 if(isFirstDataProcessPass){
514
515 isFirstDataProcessPass = false;
516 /* Start the auto home seq. */
517 startFullImagingSequence();
518 /* Once auto home seq. is started, back to previous menu */ 519 isInModifMode = false;
520 menu.menuState = AUTOMATIC_MODE_MENU;
521 menu.menuSize = 1;
522 }
523 break;
524 }

525 }
526 }
527
528
529
530
531 //____________________________________________________________________________// 532 void menuPrintProcess(STEPPER_DATA *pStepperData){
533 /* Print switch */
534 switch(menu.menuState){
535
536 case MAIN_MENU:
537 printMainMenu();
538 break;
539
540 case SETTINGS_MENU:
541 switch (menu.menuPage){
542 case 0: printParameterMenuPage0(); 543 break;
544 case 1: printParameterMenuPage1(); 545 break;
546 }
547 break;
548
549 case MOTOR_MENU:
550 switch (menu.menuPage){
551 case 0: printMotorMenu0(pStepperData); 552 break;
553 case 1: printMotorMenu1(pStepperData); 554 break;
555 }
556 break;
557
558 case LIGHT_MENU:
559 printLedsMenu();
560 break;
561
562 case BACKLIGHT_MENU:
563 printBackLightMenu();
564 break;
565
566 case CAMERA_MENU:
567 printCameraMenu();
568 break;
569
570 case SAVE_DATA_MENU:
571 printSaveDataMenu();
572 break;
573
574 case CAPTURE_MODE_MENU: 575 printChoiceSeqMenu();
576 break;
577
578 case MANUAL_MODE_MENU:
579 printManualModeMenu(pStepperData); 580 break;
581
582 case AUTOMATIC_MODE_MENU:
583 printAutoModeMenu(pStepperData); 584 break;
585
586 case ABOUT_MENU:
587 printAboutMenu();
588 break;
589
590 case AUTO_HOME_MENU:
591 printAutoHomeMenu();
592 break;
593

594 default:
595 break;
596 }
597 }
598
599
600
601
602
603
604 void printLcdInit(void){ 605
606 char str[2];
607 ClrDisplay();
608 DisplayOnOff(DISPLAY_ON); //Disable cursor 609 SetPostion(LINE1);
610 WriteString("Auto RTI Capt System");
611 SetPostion(LINE2);
612 WriteString("08-09 2023");
613 SetPostion(LINE3);
614 WriteString("Meven Ricchieri"); 615 SetPostion(LINE4);
616
617 int i;
618 for (i = 0; i < 20; i++){ 619
620 APP_Delay_ms(75);
621 SetPostion(LINE4 + i); 622 sprintf(str, "%c", 0xD0); 623 WriteString(str);
624 }
625 APP_Delay_ms(150);
626 }
627
628 void printMainMenu(void){ 629
630 ClrDisplay();
631 SetPostion(LINE1);
632 WriteString(" Capture mode"); 633 SetPostion(LINE2);
634 WriteString(" Settings"); 635 SetPostion(LINE3);
636 WriteString(" About"); 637 SetPostion(LINE4);
638 WriteString(" ");
639 }
640
641 void printParameterMenuPage0(void){ 642
643 ClrDisplay();
644 SetPostion(LINE1);
645 WriteString(" Return"); 646 SetPostion(LINE2);
647 WriteString(" Motor"); 648 SetPostion(LINE3);
649 WriteString(" Power light"); 650 SetPostion(LINE4);
651 WriteString(" Back-light"); 652 }
653
654 void printParameterMenuPage1(void){ 655
656 ClrDisplay();
657 SetPostion(LINE1);
658 WriteString(" Camera"); 659 SetPostion(LINE2);
660 WriteString(" Save data"); 661 }
662

663 void printMotorMenu0(STEPPER_DATA *pStepperData){ 664
665 char str[21];
666 ClrDisplay();
667 SetPostion(LINE1);
668 WriteString(" Return");
669 SetPostion(LINE2);
670 sprintf(str, " Speed: %4dsteps/s", pStepperData->stepPerSec); 671 WriteString(str);
672 SetPostion(LINE3);
673 | sprintf(str, " Gear: | 1:%3d", pStepperData->gearValue);
674 WriteString(str);
675 SetPostion(LINE4);
676 sprintf(str, " Step angle: %1.2f%c", pStepperData->anglePerStep, 0x01); 677 WriteString(str);
678 }
679
680 void printMotorMenu1(STEPPER_DATA *pStepperData){ 681
682 char str[21];
683 ClrDisplay();
684 SetPostion(LINE1);
685 /* A changer, en Duty pure, ensuite en %%% */
686 sprintf(str, " Power : %03d", pStepperData->dutyCycleStepper); 687 WriteString(str);
688 }
689
690 void printLedsMenu(void){ 691
692 char str[21];
693 ClrDisplay();
694 SetPostion(LINE1);
695 WriteString(" Return");
696 SetPostion(LINE2);
697 /* 0.04 = 100 / 2500 */
698 sprintf(str, " Intensity : %03.0f%%", ((float)appData.lightIntensity * 0.04)); 699 WriteString(str);
700 | // | SetPostion(LINE3);
701 | // | sprintf(str, " Light time: %03dms", appData.lightTime);
702 | // | WriteString(str);
703 }
704
705 void printChoiceSeqMenu(void){ 706
707 ClrDisplay();
708 SetPostion(LINE1);
709 WriteString(" Return"); 710 SetPostion(LINE2);
711 WriteString(" Manual mode"); 712 SetPostion(LINE3);
713 WriteString(" Auto mode"); 714 SetPostion(LINE4);
715 WriteString(" ");
716 }
717
718 void printAboutMenu(void){ 719
720 ClrDisplay();
721 SetPostion(LINE1);
722 WriteString(" Return");
723 SetPostion(LINE2);
724 WriteString(" Version 1.0.0"); 725 SetPostion(LINE3);
726 WriteString(" Meven Ricchieri"); 727 SetPostion(LINE4);
728 WriteString(" 08-09 2023");
729 }
730
731 void printManualModeMenu(STEPPER_DATA *pStepperData){

732
733 char str[21];
734 ClrDisplay();
735 SetPostion(LINE1);
736 WriteString(" Return");
737 SetPostion(LINE2);
738 if(pStepperData->isIndexed == true){
739 | sprintf(str, " Auto home | :%s", "DONE");
740 } else {
741 | sprintf(str, " Auto home | :%s", "NOK");
742 }
743 WriteString(str);
744 SetPostion(LINE3);
745 sprintf(str, " Des. angle :%03.1f%c", (((float)pStepperData->stepToReach * 1.8) 746 / pStepperData->gearValue), 0x01);
747 | // | sprintf(str, " Steps | : %05d", stepperData.stepToDoReach);
748 WriteString(str);
749 SetPostion(LINE4);
750 sprintf(str, " Real angle :%03.1f%c", (((float)pStepperData->performedSteps * 1.8) 751 / pStepperData->gearValue), 0x01);
752 | // | sprintf(str, " Steps | :%05d", pStepperData->performedStep);
753 WriteString(str);
754 }
755
756 void printAutoModeMenu(STEPPER_DATA *pStepperData){ 757
758 char str[21];
759 ClrDisplay();
760 SetPostion(LINE1);
761 WriteString(" Return");
762 SetPostion(LINE2);
763 if(appData.isFullImaginSeqEnable == false) { 764 sprintf(str, " Start sequence");
765 } else {
766 sprintf(str, " Sequence is ON");
767 }
768 WriteString(str);
769 SetPostion(LINE3);
770 | | sprintf(str, " Pictures: | %03d", appData.nbrOfShotsPerformed);
771 WriteString(str);
772 SetPostion(LINE4);
773 sprintf(str, " Real angle :%03.1f%c", (((float)pStepperData->performedSteps * 1.8) 774 / pStepperData->gearValue), 0x01);
775 WriteString(str);
776 }
777
778 void printAutoHomeMenu(void){ 779
780 ClrDisplay();
781 SetPostion(LINE1);
782 WriteString(" Return");
783 SetPostion(LINE2);
784 WriteString(" Press to index"); 785 SetPostion(LINE3);
786 WriteString(" ");
787 SetPostion(LINE4);
788 WriteString(" ");
789 }
790
791 void printBackLightMenu(void){ 792
793 char str[21];
794 ClrDisplay();
795 SetPostion(LINE1);
796 WriteString(" Return");
797 SetPostion(LINE2);
798 /* 0.04 = 100 / 2500 */
799 sprintf(str, " Intensity : %03.0f%%", ((float)appData.backLightIntensitiy * 0.04)); 800 WriteString(str);

801 }
802
803 void printCameraMenu(void){ 804
805 char str[21];
806 ClrDisplay();
807 SetPostion(LINE1);
808 WriteString(" Return");
809 SetPostion(LINE2);
810 sprintf(str, " Expos time: %04dms", appData.exposureDuration); 811 WriteString(str);
812 SetPostion(LINE3);
813 sprintf(str, " Time bw pic:%04dms", appData.timeBetweenPictures); 814 WriteString(str);
815 SetPostion(LINE4);
816 WriteString(" Trigger : cable"); // <-- or IR but not ready
817 }
818
819 void printSaveDataMenu(){
820
821 ClrDisplay();
822 SetPostion(LINE1);
823 WriteString(" Return");
824 SetPostion(LINE2);
825 WriteString(" Confirm to save"); 826 SetPostion(LINE3);
827 WriteString(" ! Old values will "); 828 SetPostion(LINE4);
829 WriteString(" be overwritten ! "); 830 }
831
832
833
834
835 /* Clear the first row all 4 lines */ 836 void clearFirstRow(void){
837
838 SetPostion(LINE1);
839 WriteString(" ");
840 SetPostion(LINE2);
841 WriteString(" ");
842 SetPostion(LINE3);
843 WriteString(" ");
844 SetPostion(LINE4);
845 WriteString(" ");
846 }
847
848 /* Print cursor */
849 void printCursor(int32_t cursor){ 850
851 char str[2];
852 clearFirstRow();
853 SetPostion(cursor * 0x20);
854 sprintf(str, "%c", RIGHT_ARROW); 855 WriteString(str);
856 }
857
858
859
860 //----------------------------------------------------------------------------// saveDataInEeprom
861 bool saveDataInEeprom(STEPPER_DATA *pStepperData){
862
863 DATA_IN_EEPROM dataToSaveInEeprom;
864
865 /* Set the structure value for saving in EEPROM */
866 | dataToSaveInEeprom.stepPerSec | = pStepperData->stepPerSec;
867 dataToSaveInEeprom.stepPerTurn = pStepperData->stepPerTurn;
868 | dataToSaveInEeprom.gearValue | = pStepperData->gearValue;

869 dataToSaveInEeprom.anglePerStep = pStepperData->anglePerStep;
870
871 | dataToSaveInEeprom.lightIntensity | = appData.lightIntensity;
872 dataToSaveInEeprom.timeBetweenPictures = appData.timeBetweenPictures;
873 | dataToSaveInEeprom.exposureDuration | = appData.exposureDuration;
874
875 dataToSaveInEeprom.backLightIntensitiy = appData.backLightIntensitiy; 876
877 dataToSaveInEeprom.controlValue = CONTROL_VALUE;
878
879 Init_DataBuff();
880 /* Write in the EEPROM */
881 NVM_WriteBlock((uint32_t*)&dataToSaveInEeprom, sizeof(dataToSaveInEeprom)); 882
883 return 0;
884 }
885
886 //----------------------------------------------------------------------------// readDataFromEeprom
887 /* Read the parameters from the EEPROM */
888 bool readDataFromEeprom(STEPPER_DATA *pStepperData){
889
890 DATA_IN_EEPROM dataReadFromEeprom;
891
892 Init_DataBuff();
893 /* Read in the EEPROM */
894 NVM_ReadBlock((uint32_t*)&dataReadFromEeprom, sizeof(dataReadFromEeprom)); 895
896 /* Check if the control value is already inside the EEPROM */
897 if(dataReadFromEeprom.controlValue == CONTROL_VALUE){
898
899 /* Save data from EEPROM */
900 | pStepperData->stepPerSec | = dataReadFromEeprom.stepPerSec;
901 | pStepperData->stepPerTurn | = dataReadFromEeprom.stepPerTurn;
902 | pStepperData->gearValue | = dataReadFromEeprom.gearValue;
903 pStepperData->anglePerStep = dataReadFromEeprom.anglePerStep;
904
905 | appData.lightIntensity | = dataReadFromEeprom.lightIntensity;
906 appData.timeBetweenPictures = dataReadFromEeprom.timeBetweenPictures;
907 | appData.exposureDuration | = dataReadFromEeprom.exposureDuration;
908
909 appData.backLightIntensitiy = dataReadFromEeprom.backLightIntensitiy; 910
911 } else {
912
913 // SAVE INIT VAL
914 saveDataInEeprom(pStepperData); 915 }
916 }

1 /*
2 | * File: | menu.h
3 * Author: ricch
4 *
5 * Created on August 30, 2023, 10:17 AM 6 */
7
8 #ifndef MENU_H
9 #define MENU_H
10
11 #ifdef __cplusplus

### 12 extern "C" {

13 #endif
14
15 #include <stdbool.h>
16 #include <stdint.h>
17 #include <stepperDriver.h> 18 #include "Mc32NVMUtil.h" 19
20 #define RIGHT_ARROW 0x10 21
22 // Enumerations
23
24 /* All menus */

### 25 typedef enum

26 {
27 MAIN_MENU = 0,
28 CAPTURE_MODE_MENU,
29 SETTINGS_MENU,
30 ABOUT_MENU,
31 MOTOR_MENU,
32 MANUAL_MODE_MENU,
33 LIGHT_MENU,
34 BACKLIGHT_MENU,
35 CAMERA_MENU,
36 SAVE_DATA_MENU,
37 AUTO_HOME_MENU,
38 AUTOMATIC_MODE_MENU,
39
40 } MENU_STATE;
41
42
43
44

### 45 typedef enum{

46
47 RETURN_SEL = 0,
48
49 } COMMON;
50

### 51 typedef enum{

52
53 CAPTURE_MODE_SEL = 0,
54 SETTINGS_SEL,
55 ABOUT_SEL,
56
57 } MAIN_MENU_LIST;
58

### 59 typedef enum{

60
61 LIGHT_INTENSITY_SEL = 1, 62 LIGHT_TIME_SEL,
63 TIME_BW_PICTURES,
64
65 }LEDS_MENU_LIST;
66

### 67 typedef enum{

68
69 AUTO_HOME_START_SEL = 1,

70
71 } AUTO_HOME_MENU_LIST;
72

### 73 typedef enum{

74
75 MANUAL_MODE_SEL = 1,
76 AUTOMATIC_MODE_SEL,
77
78 } CHOICE_SEQ_MENU_LIST; 79

### 80 typedef enum{

81
82 AUTO_HOME_SEL = 1,
83 ANGLE_SEL,
84
85 } MANUAL_MODE_MENU_LIST; 86

### 87 typedef enum{

88
89 AUTOMATIC_MODE_START_SEL = 1, 90
91 } AUTO_MODE_MENU_LIST;
92

### 93 typedef enum{

94
95 MOTOR_SEL = 1,
96 LEDS_SEL,
97 BACKLIGHT_SEL,
98 CAMERA_SEL,
99 SAVE_DATA_SEL,
100
101 } SETTINGS_MENU_LIST;
102
103 typedef enum{
104
105 SPEED_SEL = 1,
106 GEAR_SEL,
107 STEP_PER_TURN_SEL,
108 POWER_SEL,
109
110 } MOTOR_MENU_LIST;
111
112 typedef enum{
113
114 BACKLIGHT_INTENSITY_SEL = 1, 115
116 } BACKLIGHT_MENU_LIST;
117
118 typedef enum{
119
120 EXPOSURE_TIME_SEL = 1, 121 TIME_BW_PICTURES_SEL,
122
123 } CAMERA_MENU_LIST;
124
125
126
127 typedef enum{
128
129 ANGLE_MODIF = 0,
130 SPEED_MODIF,
131 GEAR_MODIF,
132 STEP_PER_TURN_MODIF,
133 POWER_MODIF,
134 BL_INTENSITY_MODIF,
135 LIGHT_INTENSITY_MODIF, 136 LIGHT_TIME_MODIF,
137 EXPOSURE_TIME_MODIF,
138 TIME_BW_PICTURES_MODIF,

139
140 SAVE_DATA_START,
141 AUTO_HOME_START,// INTERACT 142 AUTOMATIC_MODE_START,
143
144 } MODIF_LIST;
145
146
147
148 // Structures
149 typedef struct{
150
151 uint8_t menuPage;
152 uint8_t menuSize;
153 MENU_STATE menuState;
154 MODIF_LIST modifState; 155
156 } MENU;
157
158
159
160
161
162 // Prototypes
163 void printLcdInit(void);
164 void printMainMenu(void);
165 void printParameterMenuPage0(void);
166 void printParameterMenuPage1();
167 void printMotorMenu0(STEPPER_DATA *pStepperData); 168 void printMotorMenu1(STEPPER_DATA *pStepperData); 169 void printLedsMenu(void);
170 void printChoiceSeqMenu(void);
171 void printAboutMenu(void);
172 void printManualModeMenu(STEPPER_DATA *pStepperData); 173 void printAutoModeMenu(STEPPER_DATA *pStepperData); 174 void printAutoHomeMenu(void);
175 void printBackLightMenu(void);
176 void printCameraMenu(void);
177 void printSaveDataMenu(void);
178
179 void menuManagementProcess(void);
180 void menuActionProcess(int32_t pec12RotationValue);
181 void menuDataProcess(int32_t *pec12RotationValue, STEPPER_DATA *pStepperData); 182 void menuPrintProcess(STEPPER_DATA *pStepperData);
183
184 void clearFirstRow(void);
185 void printCursor(int32_t cursor);
186
187 bool saveDataInEeprom(STEPPER_DATA *pStepperData); 188 bool readDataFromEeprom(STEPPER_DATA *pStepperData); 189
190
191 #ifdef __cplusplus
192 }
193 #endif
194
195 #endif /* MENU_H */
196
197

1 /*
2 | * File: | lights.c
3 * Author: ricch
4 *
5 * Created on September 5, 2023, 7:15 PM 6 */
7
8 #include "app.h"
9
10 extern APP_DATA appData;
11
12 //----------------------------------------------------------------------------// lightManagementProcess

### 13 void sequenceManagementProcess(void){

14
15 static int32_t order = 5; //= angleDesired / gear; 16

### 17 if(appData.isFiveShotsSeqEnable){

18
19 /* Sequence of 5 pictures is enable */ 20 //fiveShotsSeqProcess();
21 //startFiveShotsSeqProcess();
22 }

### 23 if(appData.isFullImaginSeqEnable){

24
25 /* Full sequence is enable */

### 26 switch (appData.valSeq){

27

### 28 case 0:

29 | // | appData.valSeq += fiveShotsSeqProcess();
30 break;

### 31 case 1:

32 setRotationToDo(getMyStepperStruct(), &order);

### 33 if(getPerformedSteps(getMyStepperStruct()) == order){

34 order += 5; // appData.angleBwEachSeq;
35 appData.valSeq = 0;
36 appData.seqClock1_ms = 0;
37 appData.seqClock2_ms = 0;
38 startFiveShotsSeqProcess(); 39 }
40 break;
41 }
42 }
43 }
44
45
46 //----------------------------------------------------------------------------// turnOffAllPwrLeds

### 47 void turnOffAllPwrLeds(void){

48
49 /* Turn off all power LED */ 50 LED1_CMDOff();
51 LED2_CMDOff();
52 LED3_CMDOff();
53 LED4_CMDOff();
54 LED5_CMDOff();
55 }
56
57 //----------------------------------------------------------------------------// startFiveShotsSequence
58 /* Start a sequence for 5 shots */

### 59 void startFiveShotsSequence(void){

60
61 appData.seqClock1_ms = 0;
62 appData.seqClock2_ms = 0;
63 appData.isFiveShotsSeqEnable = true;
64 }
65
66 //----------------------------------------------------------------------------//

startFullImagingSequence

### 67 void startFullImagingSequence(void){

68
69 appData.seqClock1_ms = 0;
70 appData.seqClock2_ms = 0;
71 appData.isFullImaginSeqEnable = true; 72 appData.valSeq = 0;
73 appData.nbrOfShotsPerformed = 0;
74 startFiveShotsSeqProcess();
75 }
76
77 //----------------------------------------------------------------------------// simpleShotProcess

### 78 void startSimpleShotProcess(void){

79
80 appData.seqClock2_ms = 0;
81 DRV_TMR4_Start();
82 }
83

### 84 void startFiveShotsSeqProcess(void){

85
86 appData.seqClock1_ms = 0;
87 DRV_TMR0_Start();
88 }
89
90 //----------------------------------------------------------------------------// imagingSeqProcess
91 /* This function takes 5 pictures with 5 different LEDs */

### 92 bool fiveShotsSeqProcess(void){

93
94 | // | if(appData.seqClock1_ms == 0){
95 | // | appData.ledId = PWR_LED1;
96 | // | startSimpleShotProcess();
97 //
98 | // | } else if(appData.seqClock1_ms == 1 * appData.timeBetweenPictures){
99 | // | appData.ledId = PWR_LED2;
100 | // | startSimpleShotProcess();
101 //
102 | // | } else if(appData.seqClock1_ms == 2 * appData.timeBetweenPictures){
103 | // | appData.ledId = PWR_LED3;
104 | // | startSimpleShotProcess();
105 //
106 | // | } else if(appData.seqClock1_ms == 3 * appData.timeBetweenPictures){
107 | // | appData.ledId = PWR_LED4;
108 | // | startSimpleShotProcess();
109 //
110 | // | } else if(appData.seqClock1_ms == 4 * appData.timeBetweenPictures){
111 | // | appData.ledId = PWR_LED5;
112 | // | startSimpleShotProcess();
113 | // | }
114 | // | if(appData.seqClock1_ms >= 5 * appData.timeBetweenPictures){
115 //
116 | // | appData.seqClock1_ms = 0;
117 | // | appData.seqClock2_ms = 0;
118 | // | appData.isFiveShotsSeqEnable = false;
119 | // | return 1;
120 | // | }
121 | // | return 0;
122 }
123
124
125 //----------------------------------------------------------------------------// setLighIntensity
126 void setLightIntensity(int32_t *lightIntensity){
127
128 // Limit values to avoid problems
129 if(*lightIntensity < LIGHT_INTENSITY_MIN) *lightIntensity 130 = LIGHT_INTENSITY_MIN;
131 if(*lightIntensity > LIGHT_INTENSITY_MAX) *lightIntensity

132 = LIGHT_INTENSITY_MAX;
133
134 /* 25 = 2500 / 100 */
135 appData.lightIntensity = *lightIntensity * 25;
136 PLIB_MCPWM_ChannelPrimaryDutyCycleSet(MCPWM_ID_0, PWM_DIM_CH, appData.lightIntensity );
137 }
138 int32_t getLightIntensity(void){
139
140 return appData.lightIntensity / 25;
141 }
142
143 //----------------------------------------------------------------------------// setTimeBwPictures
144 void setTimeBwPictures(int32_t *timeBwPictures){
145
146 int32_t time_bw_pictures_min = appData.exposureDuration + 147 3 * MARGIN_LED_DELAY;
148 // Limit values to avoid problems
149 if(*timeBwPictures < time_bw_pictures_min) *timeBwPictures 150 = time_bw_pictures_min;
151 if(*timeBwPictures > TIME_BW_PICTURES_MAX) *timeBwPictures 152 = TIME_BW_PICTURES_MAX;
153
154 appData.timeBetweenPictures = *timeBwPictures;
155 }
156 int32_t getTimeBwPictures(void){
157
158 return appData.timeBetweenPictures;
159 }
160
161 //----------------------------------------------------------------------------// setExposureTime
162 void setExposureTime(int32_t *exposureTime){
163
164 // Limit values to avoid problems
165 if(*exposureTime < EXPOSURE_TIME_MIN) *exposureTime = EXPOSURE_TIME_MIN; 166 if(*exposureTime > EXPOSURE_TIME_MAX) *exposureTime = EXPOSURE_TIME_MAX; 167
168 appData.exposureDuration = *exposureTime;
169 }
170 int32_t getExposureTime(void){
171
172 return appData.exposureDuration; 173 }

1 /*
2 | * File: lights.h
3 * Author: ricch
4 *
5 * Created on September 5, 2023, 7:16 PM 6 */

1 /*
2 | * File: | pec12.c
3 * Author: ricch
4 *
5 * Created on August 30, 2023, 9:15 AM 6 */
7
8 #include "app.h"
9 #include "pec12.h"
10 #include "lcd_spi.h"
11
12 PEC12 pec12;
13

### 14 void scanPec12(void){

15
16 // Save old states for debounce
17 pec12.chA.state[3] = pec12.chA.state[2]; 18 pec12.chA.state[2] = pec12.chA.state[1]; 19 pec12.chA.state[1] = pec12.chA.state[0]; 20 pec12.chA.state[0] = CHANNEL_AStateGet(); 21
22 pec12.chB.state[1] = pec12.chB.state[0]; 23 pec12.chB.state[0] = CHANNEL_BStateGet(); 24
25 pec12.chC.state[3] = pec12.chC.state[2]; 26 pec12.chC.state[2] = pec12.chC.state[1]; 27 pec12.chC.state[1] = pec12.chC.state[0]; 28 pec12.chC.state[0] = PEC12R_SWStateGet();
29
30 // Check if PEC12 is in rotation

### 31 if(pec12.chA.state[0] == 0 && pec12.chA.state[1] == 0

32 && pec12.chA.state[2] == 1 && pec12.chA.state[3] == 1){ 33
34 // Check direction of rotation

### 35 if(pec12.chB.state[0] == 1 && pec12.chB.state[1] == 1){

36
37 // CW
38 pec12.incrOrDecr++;
39 | // | SetPostion(LINE3);
40 | // | sprintf(a_toPrint, "counter = %d",counter);
41 | // | WriteString(a_toPrint);
42 }

### 43 else{

44
45 //CCW
46 pec12.incrOrDecr--;
47 | // | SetPostion(LINE3);
48 | // | sprintf(a_toPrint, "counter = %d",counter);
49 | // | WriteString(a_toPrint);
50 }
51 }
52 // Check if PEC12 switch is pressed

### 53 if(pec12.chC.state[0] == 0 && pec12.chC.state[1] == 0

54 && pec12.chC.state[2] == 1 && pec12.chC.state[3] == 1){ 55
56 pec12.isPressed = true;
57 }
58 }
59

### 60 int8_t getPec12IncrOrDecr(void){

61
62 int8_t incrOrDecr = pec12.incrOrDecr; 63 pec12.incrOrDecr = 0;
64
65 return incrOrDecr;
66 }
67

### 68 int8_t getPec12SwitchEvent(void){

69

70 int8_t isPressed = pec12.isPressed; 71 pec12.isPressed = 0;
72
73 return isPressed;
74 }

1 /*
2 | * File: | pec12.h
3 * Author: ricch
4 *
5 * Created on August 30, 2023, 9:15 AM 6 */
7
8 #ifndef PEC12_H
9 #define PEC12_H
10
11 #ifdef __cplusplus

### 12 extern "C" {

13 #endif
14
15 #include <stdbool.h>
16

### 17 typedef struct

18 {
19 bool state[4];
20
21 } CHANNEL;
22

### 23 typedef struct

24 {
25 CHANNEL chA;
26 CHANNEL chB;
27 CHANNEL chC;
28 int8_t incrOrDecr;
29 bool isPressed;
30
31 } PEC12;
32
33
34
35
36 void scanPec12(void);
37 int8_t getPec12IncrOrDecr(void); 38
39
40
41
42 #ifdef __cplusplus
43 }
44 #endif
45
46 #endif /* PEC12_H */
47
48

1 /******************************************************************************* 2 System Interrupts File
3
4 File Name:
5 system_interrupt.c
6
7 Summary:
8 Raw ISR definitions.
9
10 Description:
11 This file contains a definitions of the raw ISRs required to support the 12 interrupt sub-system.
13
14 Summary:
15 This file contains source code for the interrupt vector functions in the 16 system.
17
18 Description:
19 This file contains source code for the interrupt vector functions in the 20 system. It implements the system and part specific vector "stub" functions 21 from which the individual "Tasks" functions are called for any modules
22 executing interrupt-driven in the MPLAB Harmony system.
23
24 Remarks:
25 This file requires access to the systemObjects global data structure that 26 contains the object handles to all MPLAB Harmony module objects executing 27 interrupt-driven in the system. These handles are passed into the individual 28 module "Tasks" functions to identify the instance of the module to maintain. 29 *******************************************************************************/ 30
31 // DOM-IGNORE-BEGIN
32 /******************************************************************************* 33 Copyright (c) 2011-2014 released Microchip Technology Inc. All rights reserved. 34
35 Microchip licenses to you the right to use, modify, copy and distribute
36 Software only when embedded on a Microchip microcontroller or digital signal 37 controller that is integrated into your product or third party product
38 (pursuant to the sublicense terms in the accompanying license agreement). 39
40 You should refer to the license agreement accompanying this Software for
41 additional information regarding your rights and obligations.
42
43 SOFTWARE AND DOCUMENTATION ARE PROVIDED "AS IS" WITHOUT WARRANTY OF ANY KIND, 44 EITHER EXPRESS OR IMPLIED, INCLUDING WITHOUT LIMITATION, ANY WARRANTY OF
45 MERCHANTABILITY, TITLE, NON-INFRINGEMENT AND FITNESS FOR A PARTICULAR PURPOSE. 46 IN NO EVENT SHALL MICROCHIP OR ITS LICENSORS BE LIABLE OR OBLIGATED UNDER
47 CONTRACT, NEGLIGENCE, STRICT LIABILITY, CONTRIBUTION, BREACH OF WARRANTY, OR 48 OTHER LEGAL EQUITABLE THEORY ANY DIRECT OR INDIRECT DAMAGES OR EXPENSES
49 INCLUDING BUT NOT LIMITED TO ANY INCIDENTAL, SPECIAL, INDIRECT, PUNITIVE OR 50 CONSEQUENTIAL DAMAGES, LOST PROFITS OR LOST DATA, COST OF PROCUREMENT OF
51 SUBSTITUTE GOODS, TECHNOLOGY, SERVICES, OR ANY CLAIMS BY THIRD PARTIES
52 (INCLUDING BUT NOT LIMITED TO ANY DEFENSE THEREOF), OR OTHER SIMILAR COSTS.
53 *******************************************************************************/ 54 // DOM-IGNORE-END
55
56 // ***************************************************************************** 57 // ***************************************************************************** 58 // Section: Included Files
59 // ***************************************************************************** 60 // ***************************************************************************** 61
62 #include "system/common/sys_common.h"
63 #include "app.h"
64 #include "system_definitions.h"
65 #include "lcd_spi.h"
66 #include "pec12.h"
67
68 // ***************************************************************************** 69 // *****************************************************************************

70 // Section: System Interrupt Vector Functions
71 // ***************************************************************************** 72 // ***************************************************************************** 73
74 extern APP_DATA appData;
75 extern STEPPER_DATA stepperData;
76
77 //----------------------------------------------------------------------------// TMR ID 1 78 /* This timer clocks the capture sequence */
79 /* Frequency = 1000Hz */

### 80 void __ISR(_TIMER_1_VECTOR, ipl1AUTO) IntHandlerDrvTmrInstance0(void){

81
82 PLIB_INT_SourceFlagClear(INT_ID_0,INT_SOURCE_TIMER_1);
83
84 /* Control sequence of the 5 LEDs */

### 85 if(appData.seqClock1_ms == 0){

86 appData.ledId = PWR_LED1;
87 startSimpleShotProcess();
88
89 } else if(appData.seqClock1_ms == 1 * appData.timeBetweenPictures){ 90 appData.ledId = PWR_LED2;
91 startSimpleShotProcess();
92
93 } else if(appData.seqClock1_ms == 2 * appData.timeBetweenPictures){ 94 appData.ledId = PWR_LED3;
95 startSimpleShotProcess();
96
97 } else if(appData.seqClock1_ms == 3 * appData.timeBetweenPictures){ 98 appData.ledId = PWR_LED4;
99 startSimpleShotProcess();
100
101 } else if(appData.seqClock1_ms == 4 * appData.timeBetweenPictures){ 102 appData.ledId = PWR_LED5;
103 startSimpleShotProcess();
104 }
105 if(appData.seqClock1_ms >= 5 * appData.timeBetweenPictures){ 106
107 DRV_TMR0_Stop();
108 appData.seqClock1_ms = 0;
109 appData.isFiveShotsSeqEnable = false; 110 appData.valSeq = 1;
111 //return 1;
112 } else {
113 appData.seqClock1_ms++; 114 }
115 }
116
117 //----------------------------------------------------------------------------// TMR ID 2 118 /* This timer clocks the main state machine */
119 /* Frequency = 10000Hz */
120 void __ISR(_TIMER_2_VECTOR, ipl1AUTO) IntHandlerDrvTmrInstance1(void){
121
122 PLIB_INT_SourceFlagClear(INT_ID_0,INT_SOURCE_TIMER_2);
123
124 /* States machines update */
125 APP_UpdateAppState(APP_STATE_SERVICE_TASKS);
126 }
127
128 //----------------------------------------------------------------------------// TMR ID 3 129 /* This timer clocks the stepper sequence */
130 /* Variable frequency */
131 void __ISR(_TIMER_3_VECTOR, ipl4AUTO) IntHandlerDrvTmrInstance2(void){
132
133 | // | SIGN_LED_CMDOff();
134 PLIB_INT_SourceFlagClear(INT_ID_0,INT_SOURCE_TIMER_3);
135
136 changeSpeed(getMyStepperStruct());
137 processStepper(getMyStepperStruct());
138 | // | SIGN_LED_CMDOn();

139 }
140
141 //----------------------------------------------------------------------------// TMR ID 4 142 /* This timer is used for the APP_Delay_ms() function */
143 /* Frequency = 1000Hz */
144 void __ISR(_TIMER_4_VECTOR, ipl1AUTO) IntHandlerDrvTmrInstance3(void){
145
146 PLIB_INT_SourceFlagClear(INT_ID_0,INT_SOURCE_TIMER_4);
147
148 /* Timer for ms delay */
149 appData.msCounter++;
150 }
151
152 //----------------------------------------------------------------------------// TMR ID 5 153 /* Frequency = 1000Hz */
154 void __ISR(_TIMER_5_VECTOR, ipl3AUTO) IntHandlerDrvTmrInstance4(void)
155 {
156 PLIB_INT_SourceFlagClear(INT_ID_0,INT_SOURCE_TIMER_5);
157
158 //------------------------------------------------------------------------// Start of sequence
159 if(appData.seqClock2_ms == 0){
160
161 switch (appData.ledId){ 162 /* Turn on LED */
163 case PWR_LED1:
164 turnOffAllPwrLeds();
165 LED1_CMDOn();
166 break;
167
168 case PWR_LED2:
169 turnOffAllPwrLeds();
170 LED2_CMDOn();
171 break;
172
173 case PWR_LED3:
174 turnOffAllPwrLeds();
175 LED3_CMDOn();
176 break;
177
178 case PWR_LED4:
179 turnOffAllPwrLeds();
180 LED4_CMDOn();
181 break;
182
183 case PWR_LED5:
184 turnOffAllPwrLeds();
185 LED5_CMDOn();
186 break;
187 }
188 }
189 if(appData.seqClock2_ms == MARGIN_LED_DELAY){ 190
191 /* Capture the target */
192 FOCUS_CMDOn();
193 TRIGGER_CMDOn();
194 appData.nbrOfShotsPerformed++;
195 | // | SIGN_LED_CMDOn();
196 }
197 if(appData.seqClock2_ms == appData.exposureDuration + MARGIN_LED_DELAY){ 198
199 TRIGGER_CMDOff();
200 FOCUS_CMDOff();
201 }
202 //------------------------------------------------------------------------// End of
| | sequence
203 if(appData.seqClock2_ms >= appData.exposureDuration + (2 * MARGIN_LED_DELAY)){ 204
205 /* Turn off TMR4 */

206 DRV_TMR4_Stop();
207 turnOffAllPwrLeds();
208 appData.seqClock2_ms = 0;
209 appData.ledId = ALL_LED_DISABLE; 210 } else {
211 appData.seqClock2_ms++;
212 }
213 }
214 /******************************************************************************* 215 End of File
216 */
217

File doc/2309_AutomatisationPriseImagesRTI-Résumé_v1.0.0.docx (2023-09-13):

RESUMÉ - Travail de diplôme Meven Ricchieri

SLO

2023

Titre :

2309_AutomatisationPriseImagesRTI_v1.0.0

Contexte et objectifs :

Ce projet de diplôme vise à concevoir un système automatisé pour faciliter la capture d'images RTI (Reflectance Transformation Imaging). Il est divisé en deux parties distinctes : la réalisation électronique, gérée par l'auteur du projet, et la réalisation mécanique, confiée à un étudiant en génie mécanique. La partie électronique gère les LEDs de puissance pour un éclairage optimal, le moteur pour le positionnement précis et la coordination des prises de vue. En collaboration avec le Musée MCAH (Musée des Arts et de la Culture Historique), ce projet a été mandaté pour améliorer la documentation des collections d'art et d'objets historiques du musée.

Résultats obtenus et conclusion :

Le En date du 13 septembre 2023, le projet est accompli à hauteur d'environ 90%. Les modes de fonctionnement manuel et automatique sont parfaitement opérationnels. L'utilisateur peut aisément configurer les paramètres de la séquence, tels que le temps entre chaque prise de vue, la durée de l'éclairage et l'angle de rotation du moteur entre chaque série de 5 prises, pour n'en citer que trois. De plus, la possibilité de sauvegarder ces paramètres dans l'EEPROM, assurant leur restauration à chaque démarrage, est implémentée. Les tests ont confirmé que le déclenchement de l'appareil photo Nikon D750 fonctionne comme prévu.

En résumé, le montage a été mis en service avec succès, bien que des difficultés aient surgi lors de la phase de contrôle du moteur, entraînant une perte de temps significative. Heureusement, ces problèmes ont été résolus.

Cependant, un problème subside, le courant sortant du driver de LED de puissance est inférieur à la valeur qui était initialement prévue. Des recherches à ce niveau-là sont nécessaires.

Enseignant de diplôme: M. Serge Castoldi

Entreprise mandante: MCAH / M. Mathieu Bernard-Reymond

Ecole supérieure, école des métiers Lausanne Version 2.2 Rue de Sébeillon 12 du 02.09.2021 CH-1004 Lausanne www.etml-es.ch Résumé DIPLOME TYPE_v2-2 | 1 / 1 |

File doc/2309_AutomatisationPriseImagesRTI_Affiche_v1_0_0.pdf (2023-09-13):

### Meven Ricchieri

TECHNICIEN-NE ES EN GÉNIE ÉLECTRIQUE / 2023

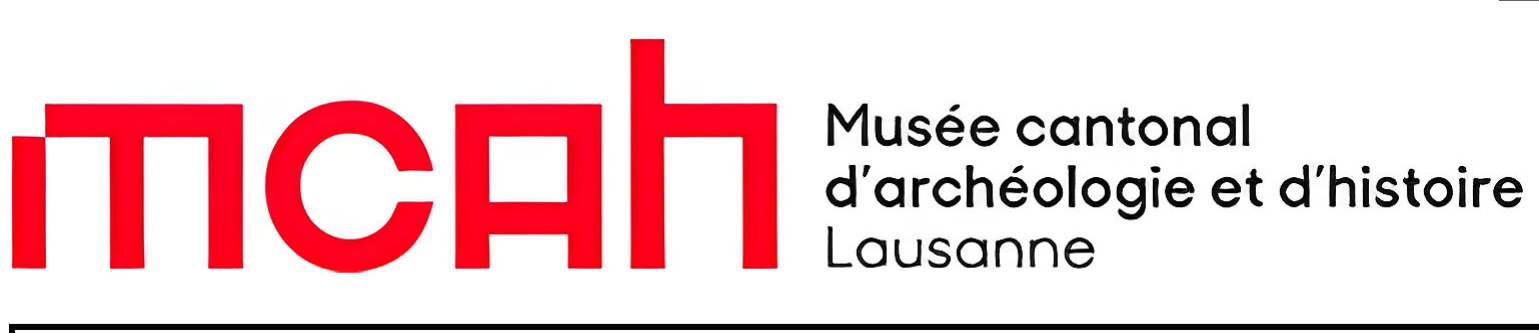
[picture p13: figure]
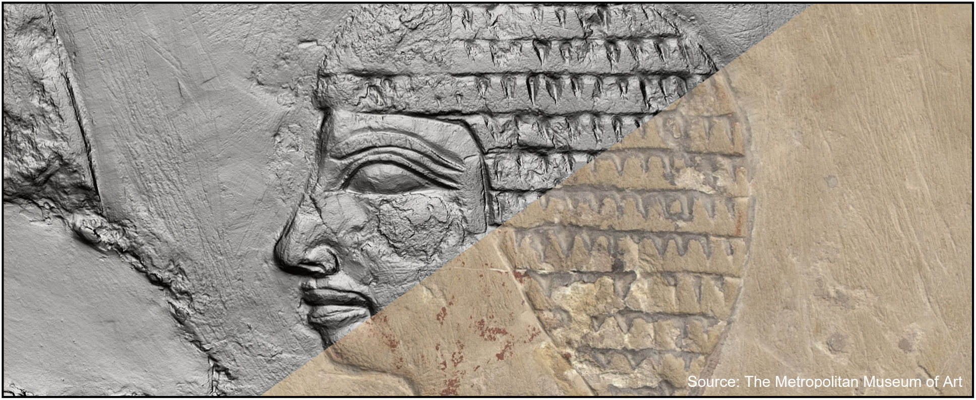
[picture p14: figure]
Source: The Metropolitan Museum of Art

## www.etml-es.ch

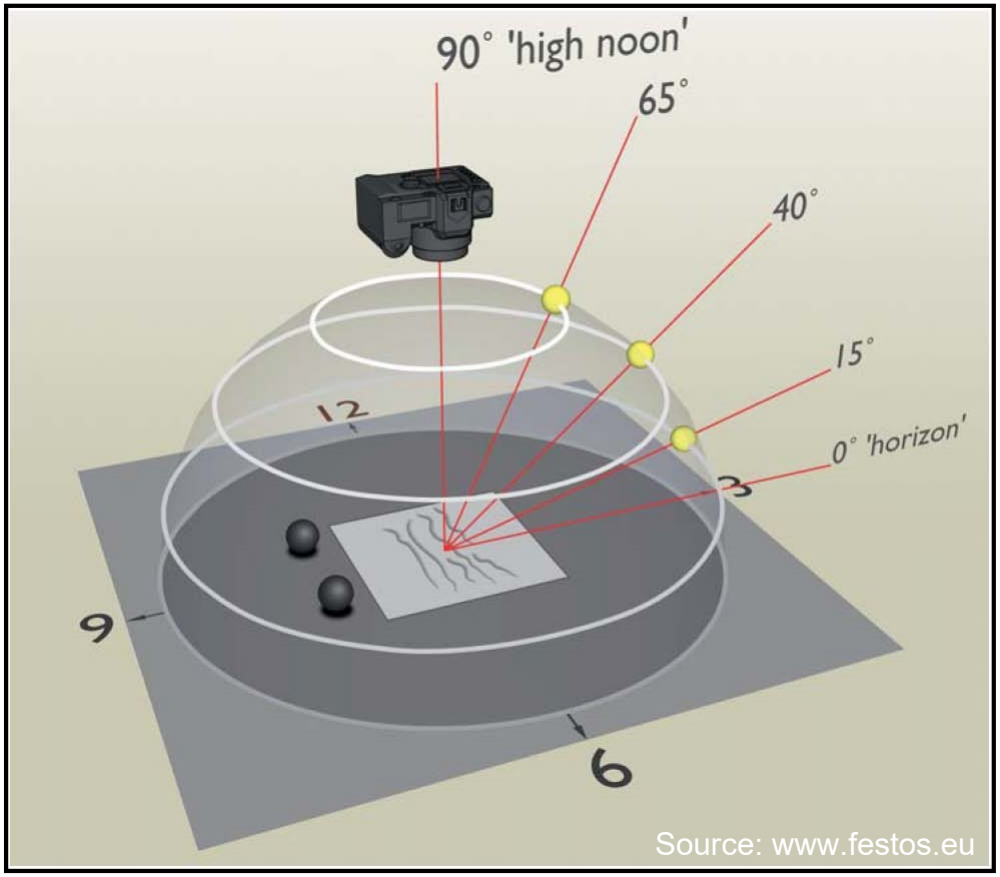
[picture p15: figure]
Source: www.festos.eu

rue de Sébeillon 12, 1004 Lausanne | ETML

2309_AutomatisationPriseImagesRTI_v1.0.0

Ce projet de diplôme vise à concevoir un système automatisé pour faciliter la capture d'images RTI (Reflectance Transformation Imaging). Il est divisé en deux parties distinctes : la réalisation électronique, réalisée par moi-même, et la réalisation mécanique, confiée à un diplômant en génie mécanique. La partie électronique gère les LEDs de puissance pour un éclairage optimal de l’artéfact, le moteur pour le positionnement précis et la coordination des prises de vue. En collaboration avec le musée cantonal d’archéologie et d’histoire (MCAH), ce projet a été mandaté pour améliorer la documentation des collections d'art et d'objets historiques.

J'ai grandement apprécié l'opportunité de mener à bien ce projet. Actuellement, bien que quelques détails restent à finaliser, nous sommes sur la voie de concrétiser notre objectif de mettre ce système en service au musée dans les mois à venir. Cette expérience m'a permis d'appliquer mes compétences techniques avancées en électronique et en mécanique tout en soulignant l'importance de la collaboration interdisciplinaire. Je suis convaincu que le résultat final sera un atout précieux pour le musée MCAH, améliorant significativement leur capacité à documenter leurs collections d'art et d'objets historiques. Je tiens à exprimer ma gratitude envers toutes les personnes qui ont contribué à la réalisation de ce projet et je suis impatient de voir son déploiement au musée dans un futur proche.

La RTI (Reflectance Transformation Imaging) est une technique informatique de photographie qui capture à la fois la forme et la couleur d'un sujet, permettant un ré-éclairage interactif de toutes les directions possibles. Elle améliore mathématiquement les caractéristiques de surface et révèle des informations invisibles à l'œil nu. Les images RTI résultent de multiples photographies numériques, projetant la lumière depuis des directions différentes, créant une séquence d'images avec des variations d'ombres et de lumières. Ces images sont synthétisées mathématiquement pour créer un modèle de surface. Chaque pixel de l'image RTI contient des informations de réflectance extrapolées de la forme 3D du sujet, permettant une interaction avec la lumière virtuelle pour révéler les détails de la surface.

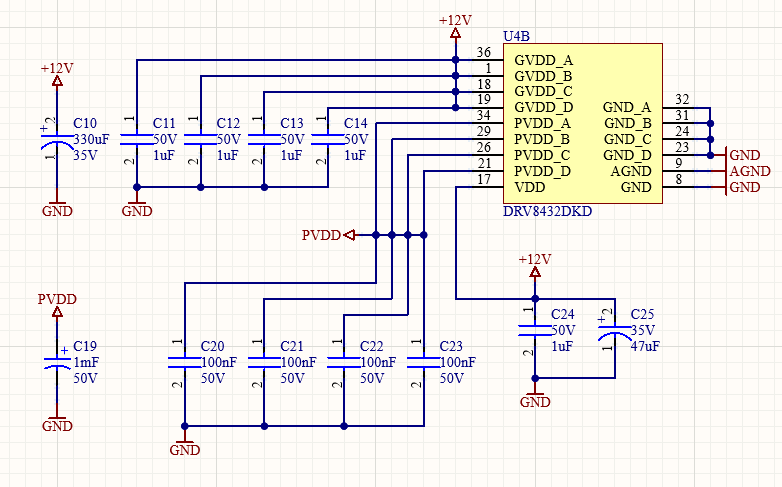
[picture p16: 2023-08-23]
doc/Images/Schematique/MotorDriverB.PNG

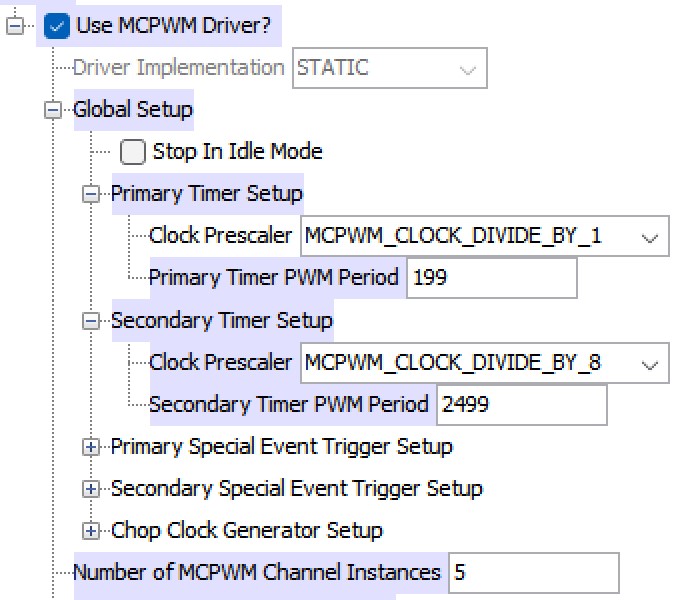
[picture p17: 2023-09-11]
doc/Mesures/DRV_MCPWM/Config3_global.jpg

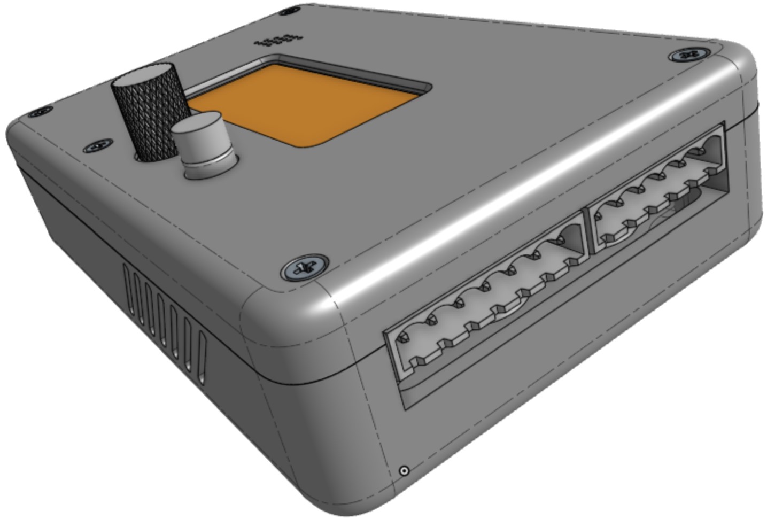
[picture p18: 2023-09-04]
doc/Images/Boîtier/CaseRightView.jpg

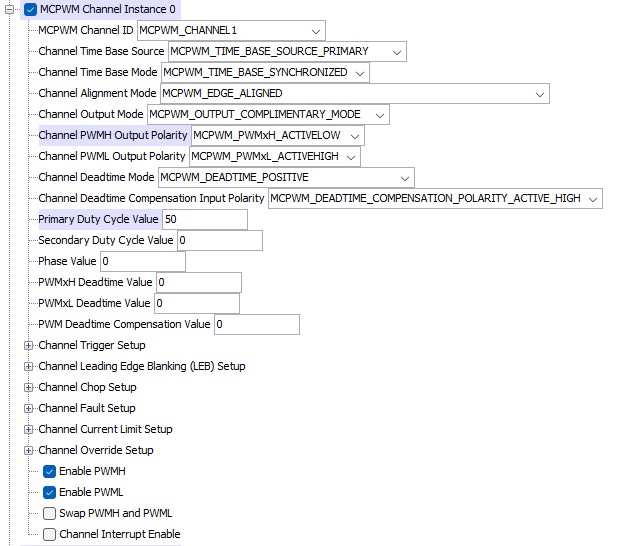
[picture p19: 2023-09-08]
doc/Mesures/DRV_MCPWM/Config2_CH1_50kHz_D94%.jpg

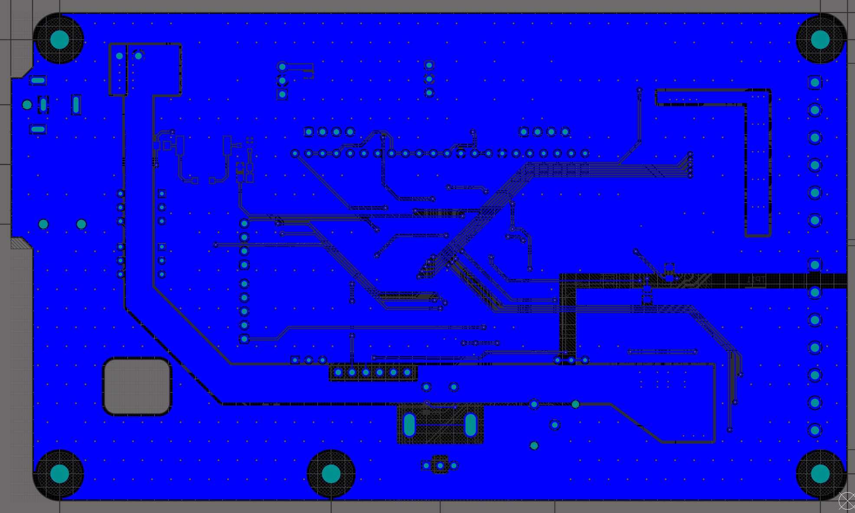
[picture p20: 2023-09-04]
doc/Images/PCB/PlanDeMasseBot.jpg

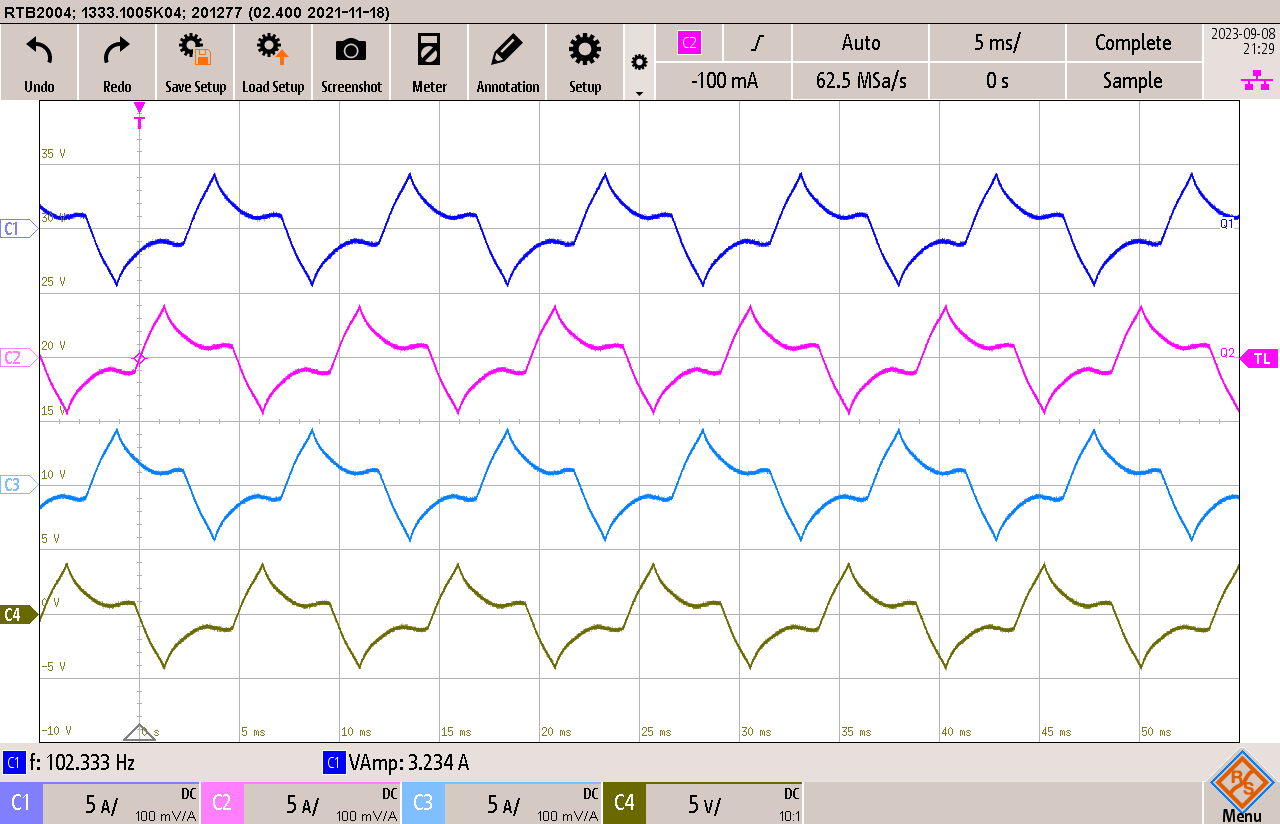
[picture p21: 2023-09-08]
doc/Mesures/DRV_MCPWM/Config2_50kHz_D94%.png

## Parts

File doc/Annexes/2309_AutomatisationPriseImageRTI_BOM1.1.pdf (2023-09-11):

Name | Description | Designator | sur PCB | Stock ES | Manufacturer 1 | Manufacturer Part Number 1 Manufacturer Lifecycle 1 | | Supplier 1 | Supplier Part Number 1 | Quantity | Supplier Unit Price 1 | Supplier Subtotal 1
Solder bridge 3mm close | | SB1, SB3 | | Y | | | | | | 2
Solder bridge 3mm open | | SB2 | | Y | | | | | | 1
4714 | JST-PH 2-PIN JUMPER CABLE - 100M | | N | N | Adafruit Industries4714 | | Unknown | Mouser | 485-4714 | 0 | 0 | 0
CRCW0805210RFKEA | | R27, R32 | | Y | Bourns | CR0805-FX-2100ELF | Volume Production | Digi-Key | 118-CR0805-FX-2100ELFDKR-ND 2 | | 0.1 | 0.2
PEC12R-4220F-S0024 | ROTARY ENCODER MECHANICAL 24PPR | ENC1 | | Y | Bourns | PEC12R-4220F-S0024 | Volume Production | Digi-Key | PEC12R-4220F-S0024-ND | 1 | 1.62 | 1.62
P7812-2000R-S | | U3 | | N | CUI | P7812-2000R-S | Unknown | Digi-Key | 102-P7812-2000R-S-ND | 1 | 5.96 | 5.96
HSB06-181810 | Dissipateur thermique BGA Alliage d’aluminium 3,2W à 75°C Montage supérieur | | N | N | CUI Devices | HSB06-181810 | Unknown | Digi-Key | 2223-HSB06-181810-ND | 0 | 0 | 0
PJ-063AH | Through Hole Right Angle DC Power Jack, 8 A, 2 mm Center Pin, 2 Position, -25 to 85 degC, RoHS, Bulk J2 | | | N | CUI Devices | PJ-063AH | Volume Production | Digi-Key | CP-063AH-ND | 1 | 1.55 | 1.55
SJ-3523-SMT-TR | | J5 | | N | CUI Devices | SJ-3523-SMT-TR | Volume Production | Digi-Key | CP-3523SJDKR-ND | 1 | 1.01 | 1.01
1N4148W-13-F | DIODE GEN PURP 100V 150MA SOD123 | D4 | N | N | Diodes | 1N4148W-13-F | Volume Production | Digi-Key | 1N4148W-13FDICT-ND | 1 | 0.18 | 0.18
PDS1040L-13 | DIODE SCHOTTKY 40V 10A POWERDI5 | D1 | | N | Diodes | PDS1040L-13 | Volume Production | Digi-Key | PDS1040LDICT-ND | 1 | 1 | 1
EA DOGM204W-A | | DS1 | | Y | Display Visions | EADOGM204W-A | Unknown | Digi-Key | 1481-1087-ND | 1 | 26.64 | 26.64
EA LED66X40-A | | | | Y | EA LED66X40-A | EA LED66X40-A | Manual Solution | Digi-Key | 1481-1166-ND | 1 | 8.07 | 8.07
RR11132211 | | | N | N | E-Switch | RR11132211 | Volume Production | Mouser | 612-RR11132211 | 1 | 0.49 | 0.49
PTS526SK15SMTR2LFS | TACT 5.2 X 5.2, 1.5 MM H, 260GF, | SW2 | | N | ITT C&K | PTS526SK15SMTR2LFS | Unknown | Newark | 35AH5137 | 1 | 0.055 | 0.055
C0805C103J5RAC7210 | CAP CER SMD 0805 .01UF X7R 5% 50 | C33, C34 | | N | KEMET | C0805C103J5RAC7210 | Volume Production | Digi-Key | 399-17616-1-ND | 2 | 0.1 | 0.2
5019 | Test Point, 1 Position SMD, RoHS, Tape and Reel | TP1, TP2, TP3, TP4, TP5, TP6, TP7, TP8, TP9, TP10, TP11, TP12, TP13, TP14, TP15, TP16, TP17, TP18, TP19 N | | | Keystone Electronics 5019 | | Volume Production | Digi-Key | 36-5019CT-ND | 19 | 0.34 | 6.46
RK73B2ATTD1R0J | | R2 | | N | KOA Speer | RK73B2ATTD1R0J | Volume Production | Digi-Key | 2019-RK73B2ATTD1R0JCT-ND | 1 | 0.1 | 0.1
RK73B2ATTD200J | | R26 | | N | KOA Speer | RK73B2ATTD200J | Volume Production | Digi-Key | 2019-RK73B2ATTD200JCT-ND | 1 | 0.1 | 0.1
59145-010 | Reed contact | | N | N | Littelfuse Hamlin | 59145-010 | Volume Production | Digi-Key | F8075-ND | 1 | 3.36 | 3.36
PIC32MK0512MCF064-I/PT | | U5 | | Y | Microchip | PIC32MK0512MCF064-I/PT | Volume Production | Digi-Key | PIC32MK0512MCF064-I/PT-ND | 1 | 9.26 | 9.26
PKMCS0909E4000-R1 | AUDIO PIEZO TRANSDUCER 12.5V SMD | LS1 | | N | Murata | PKMCS0909E4000-R1 | Volume Production | Digi-Key | 490-9647-1-ND | 1 | 0.88 | 0.88
PMV20ENR | MOSFET N-CH 30V SOT23 | Q1, Q2, Q3, Q4, Q5, Q6, Q8, Q9, Q11, Q12 | | N | Nexperia | PMV20ENR | Volume Production | Digi-Key | 1727-2301-1-ND | 10 | 0.288 | 2.88
BAT54SLT1G | DIODE ARRAY SCHOTTKY 30V SOT23-3 | D2 | | N | ON SemiconductorBAT54SLT1G | | Volume Production | Digi-Key | BAT54SLT1GOSCT-ND | 1 | 0.15 | 0.15
4N25M | 4N25M Optocoupler DC-IN 1-CH Transistor With Base DC-OUT 6-Pin PDIP Tube - Bulk | Q7, Q10 | | N | ON Semiconductor / Fairchild 4N25M | | Volume Production | Newark | 98K9084 | 2 | 0.229 | 0.458
LH R974-LP-1 | LED RED DIFFUSED 0805 SMD | D3 | | Y | Osram Opto | LH R974-LP-1 | Volume Production | | | 1
EEE-1VA101XP | CAP ALUM 100UF 20% 35V SMD | C5 | | N | Panasonic | EEE-1VA101XP | Volume Production | Digi-Key | PCE3951CT-ND | 1 | 0.5 | 0.5
EEE-1VA331P | CAP ALUM 330UF 20% 35V SMD | C10 | | N | Panasonic | EEE-1VA331P | Volume Production | Mouser | 667-EEE-1VA331P | 1 | 0.66 | 0.66
EEE-FK0J221P | CAP ALUM 220UF 20% 6.3V SMD | C6 | | N | Panasonic | EEE-FK0J221P | Volume Production | Mouser | 667-EEE-FK0J221P | 1 | 0.42 | 0.42
EEEFP1V470AP | CAP ALUM 47UF 20% 35V SMD | C25 | | N | Panasonic | EEEFP1V470AP | Volume Production | Digi-Key | PCE4552DKR-ND | 1 | 0.52 | 0.52
ERJ6ENF18R0V | | R21 | | Y | Panasonic | ERJ-6ENF18R0V | Volume Production | Digi-Key | P18.0CCT-ND | 1 | 0.1 | 0.1
ERJ6ENF2200V | | R6, R7, R8, R12, R13, R22, R28, R30, R33, R35 | | Y | Panasonic | ERJ-6ENF2200V | Volume Production | Digi-Key | P220CCT-ND | 10 | 0.079 | 0.79
ERJ6ENF5602V | | R3 | | Y | Panasonic | ERJ-6ENF5602V | Volume Production | Digi-Key | P56.0KCCT-ND | 1 | 0.1 | 0.1
S2B-PH-SM4-TB(LF)(SN) | Male Header, Pitch 2 mm, 1 x 2 Position, Height 5.5 mm, -25 to 85 degC, RoHS, Tape and Reel | J3, J4 | | N | S2B-PH-SM4-TB | S2B-PH-SM4-TB | Manual Solution | Digi-Key | 455-S2B-PH-SM4-TBDKR-ND | 2 | 0.53944 | 1.08
CL21A106KOQNNNE | CL21 Series 0805 10uF 16V ±10% Tolerance X5R Multilayer Ceramic Chip Capacitor | C1, C4 | | N | Samsung | CL21A106KOQNNNE | Volume Production | Digi-Key | 1276-1096-1-ND | 2 | 0.1 | 0.2
CL21A226MAYNNNE | CL21 Series 0805 22uF 25V ±20% Tolerance X5R Multilayer Ceramic Chip Capacitor | C8 | | N | Samsung | CL21A226MAYNNNE | Volume Production | Digi-Key | 1276-CL21A226MAYNNNECT-ND 1 | | 0.25 | 0.25
CL21B104KBCNNNC | CL21 Series 0805 100nF 50V ±10% Tolerance X7R Multilayer Ceramic Chip Capacitor | C2, C3, C9, C15, C16, C17, C18, C20, C21, C22, C23, C35, C36, C37, C38, C39, C40 N | | | Samsung | CL21B104KBCNNNC | Volume Production | Digi-Key | 1276-1003-1-ND | 17 | 0.044 | 0.748
CL21B105KBFNNNG | CL21 Series 0805 1uF 50V ±10% Tolerance X7R Multilayer Ceramic Chip Capacitor | C11, C12, C13, C14, C24 | | N | Samsung | CL21B105KBFNNNG | Volume Production | Digi-Key | 1276-6470-6-ND | 5 | 0.11 | 0.55
CL21F105ZAFNNNF | CL21 Series 0805 1uF 25V -20/+80% Tolerance Y5V Multilayer Ceramic Chip Capacitor | C26, C27, C28, C29, C30, C31, C32 | | Y | Samsung | CL21F105ZAFNNNF | Volume Production | | | 7
1241.1082.71 | | S1 | | Y | Schurter | 1241.1082.71 | Volume Production | Digi-Key | 486-7033-ND | 1 | 4.17 | 4.17
ERJ-L06UF66MV | Resistor | R1 | | N | Susumu | RL1220T-R068-G | Volume Production | Digi-Key | RL12T.068GCT-ND | 1 | 0.38 | 0.38
GMK325BJ226MM-P | None | C7 | | N | Taiyo Yuden | GMK325BJ226MM-P | Unknown | Digi-Key | 587-5853-1-ND | 1 | 0.96 | 0.96
DRV8432DKD | 12 A Dual Brushed DC or Single Bipolar Stepper Motor Driver (PWM Ctrl), 0 to 52.5 V, -40 to 85 degC, 36-pin SOP (DKD36), Green (RoHS & no Sb/Br) U4 | | | N | Texas InstrumentsDRV8432DKD | | Volume Production | | | 1
TPS92200D1DDCR | TPS92200D1DDCR | U1 | | N | Texas InstrumentsTPS92200D1DDCR | | Volume Production | Digi-Key | 296-TPS92200D1DDCRCT-ND | 1 | 1.2 | 1.2
TG-A1250-15-15-1.0 | THERM PAD 15MMX15MM GREEN | | N | N | T-Global TechnologyTG-A1250-15-15-1.0 | | Unknown | Digi-Key | 1168-TG-A1250-15-15-1.0-ND | 0 | 0 | 0
CQY36N | | | N | N | Vishay Semiconductors CQY36N | | Volume Production | Arrow Electronics CQY36N | | 1 | 0.5953 | 0.5953
173950378 | 173950378 Module DC-DC 1-OUT 3.3V 0.5A 3-Pin SIP Module Tube | U2 | | N | Wurth Electronics173950378 | | Volume Production | Digi-Key | 732-8242-5-ND | 1 | 6.34 | 6.34
7440430012 | | L1 | | N | Wurth Electronics7440430012 | | Volume Production | Digi-Key | 732-1093-1-ND | 1 | 1.53 | 1.53
61300411121 | | P4, P6, P7 | | N | Wurth Electronics61300411121 | | Volume Production | Digi-Key | 732-5317-ND | 3 | 0.19 | 0.57
61300511121 | | P3 | | N | Wurth Electronics61300511121 | | Volume Production | Digi-Key | 732-5318-ND | 1 | 0.26 | 0.26
61300611121 | | P5 | | N | Wurth Electronics61300611121 | | Volume Production | Digi-Key | 732-5319-ND | 1 | 0.35 | 0.35
691214110002 | | J1 | | N | Wurth Electronics691214110002 | | Volume Production | Digi-Key | 732-2747-ND | 1 | 0.88 | 0.88
691313510006 | | P1 | | N | Wurth Electronics691313510006 | | Volume Production | Digi-Key | 732-2074-ND | 1 | 1.32 | 1.32
691313510007 | | P2 | | N | Wurth Electronics691313510007 | | Unknown | Digi-Key | 732-691313510007-ND | 1 | 1.69 | 1.69
691351500006 | 6 poles connector | | N | N | Wurth Electronics691351500006 | | Volume Production | Digi-Key | 732-2044-ND | 1 | 3.82 | 3.82
691351500007 | 7 poles connector | | N | N | Wurth Electronics691351500007 | | Volume Production | Digi-Key | 732-691351500007-ND | 1 | 4.35 | 4.35
865080663020 | 865080663020 WCAP-ASLI Aluminum Electrolytic Capacitors | C19 | | N | Wurth Electronics865080663020 | | Volume Production | Digi-Key | 732-8465-1-ND | 1 | 2.92 | 2.92
XHP50B-00-0000-0D0BJ40CB-SB01 Power LED mounted on a PCB | | | N | N | XHP50B-00-0000-0D0BJ40CB-SB01 XHP50B-00-0000-0D0BJ40CB-SB01 Manual Solution | | | Digi-Key | 1672-1076-ND | 5 | 12.29 | 61.44
RC0805FR-071KL | Chip Resistor, 1 KOhm, +/- 1%, 125 mW, -55 to 155 degC, 0805 (2012 Metric), RoHS, Tape and Reel | R39, R40 | | Y | Yageo | RC0805FR-071KL | Volume Production | Digi-Key | 311-1.00KCRCT-ND | 2 | 0.1 | 0.2
RC0805FR-0747KL | Chip Resistor, 47 KOhm, +/- 1%, 0.125 W, -55 to 155 degC, 0805 (2012 Metric), RoHS, Tape and Reel | R9, R10, R11, R14, R15, R20, R23, R24, R29, R31, R34, R36 Y | | | Yageo | RC0805FR-0747KL | Volume Production | Digi-Key | 311-47.0KCRCT-ND | 12 | 0.024 | 0.288
RC0805JR-070RL | Chip Resistor, 0 Ohm, Jumper, +/- 5%, 0.125 W, -55 to 155 degC, 0805 (2012 Metric), RoHS, Tape and Reel R38, R42 | | | Y | Yageo | RC0805JR-070RL | Volume Production | Digi-Key | 311-0.0ARCT-ND | 2 | 0.1 | 0.2
RC0805JR-0710KL | Chip Resistor, 10 KOhm, +/- 5%, 0.125 W, -55 to 155 degC, 0805 (2012 Metric), RoHS, Tape and Reel | R4, R5, R16, R17, R18, R19, R37, R41 | | Y | Yageo | RC0805JR-0710KL | Volume Production | Digi-Key | 311-10KARCT-ND | 8 | 0.022 | 0.22
RC0805JR-0775RL | | R25 | | Y | Yageo | RC0805JR-0775RL | Volume Production | Digi-Key | 311-75ARCT-ND | 1 | 0.1 | 0.1

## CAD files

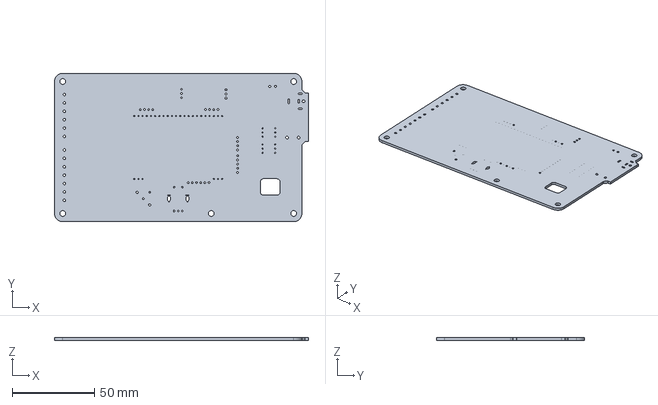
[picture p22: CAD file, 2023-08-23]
hard/Altium/2309_AutomatisationPriseImageRTI.stp
154.0 x 90.0 x 1.61 mm

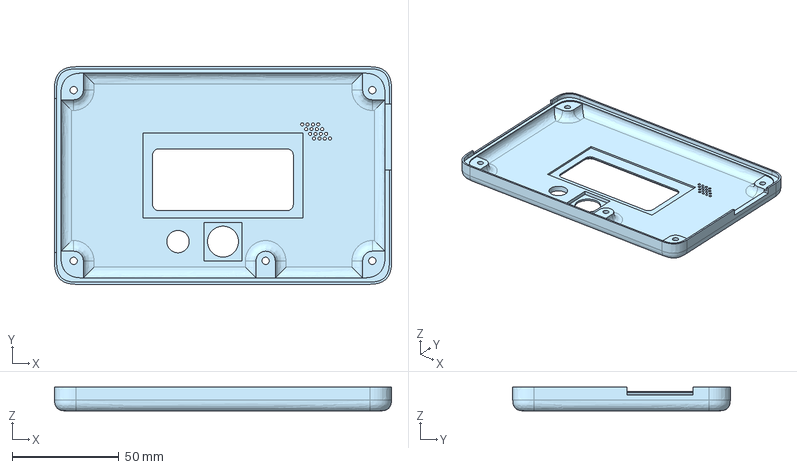
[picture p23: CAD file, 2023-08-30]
meca/Boitier/PartieHaute.step
158.0 x 102.0 x 11.1 mm

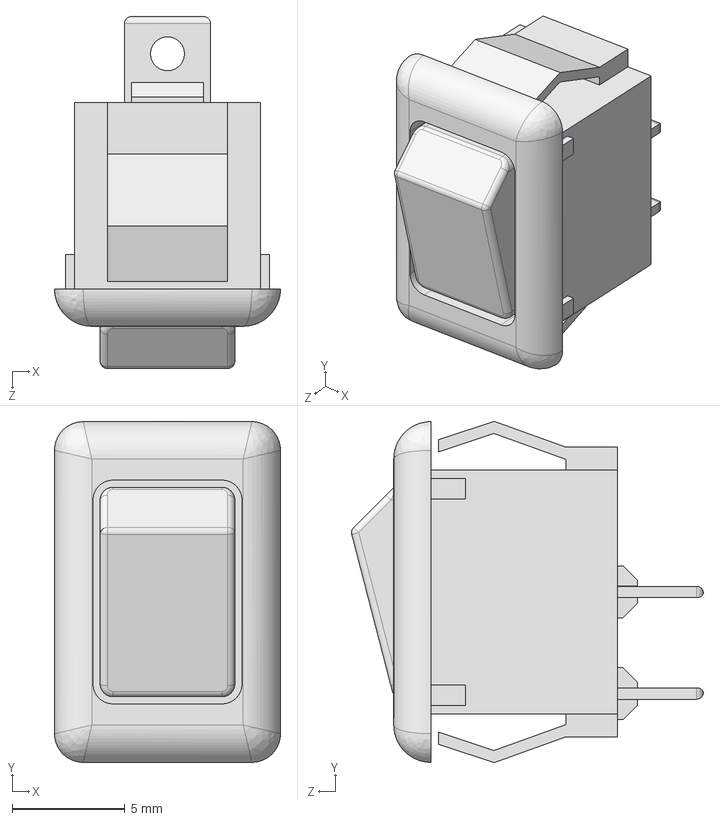
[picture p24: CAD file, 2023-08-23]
meca/PRK22J5DBBNN--3DModel-STEP-96511.STEP
10.0 x 15.1 x 15.6 mm

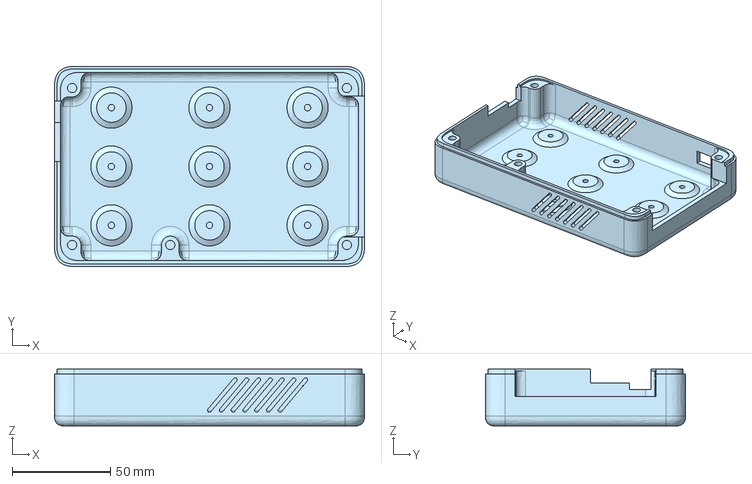
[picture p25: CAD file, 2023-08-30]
meca/Boitier/PartieBasse.step
158.0 x 102.0 x 29.0 mm

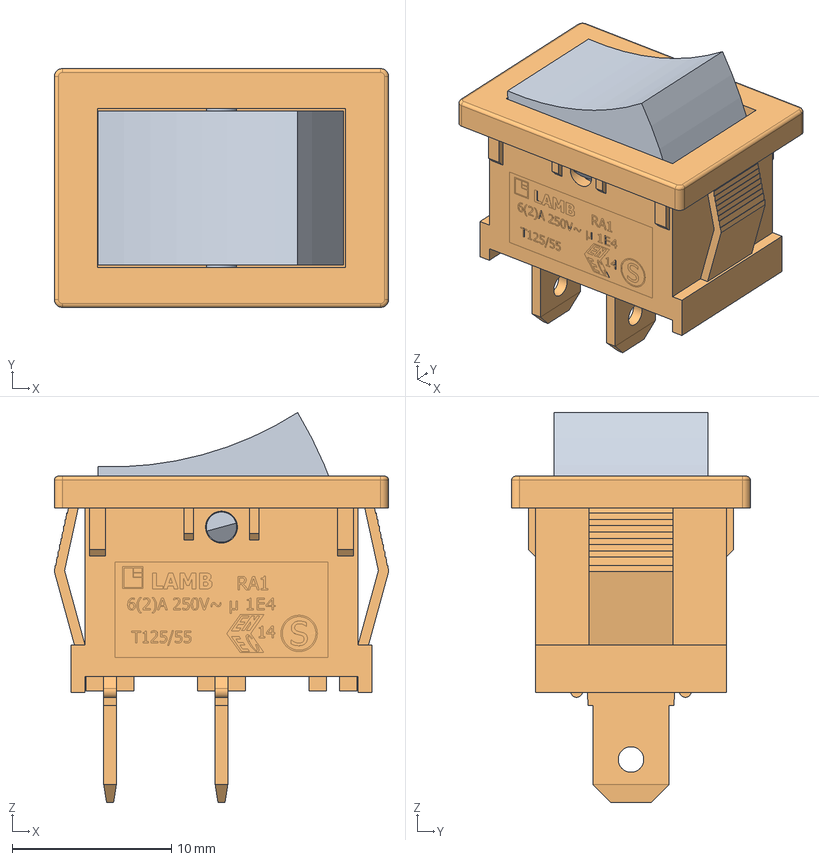
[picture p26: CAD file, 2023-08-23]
meca/RA1113xx00.stp
21.0 x 15.0 x 24.5 mm

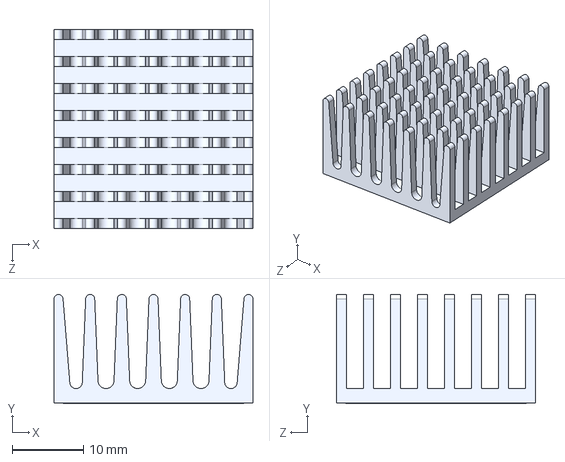
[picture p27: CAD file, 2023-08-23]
meca/658-60ABT1E HEATSINK CPU 28MM SQ BLK W-TAPE.step
27.9 x 15.3 x 27.9 mm

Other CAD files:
meca/Boitier/PartieBasse.stl
meca/Boitier/PartieHaute.stl

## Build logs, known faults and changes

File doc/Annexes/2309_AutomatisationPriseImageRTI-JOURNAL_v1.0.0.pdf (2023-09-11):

Jour | Date | Nbr période | Tâches effectuées | Nbr de café
Lundi | 07/08/2023 | 7 | Réception et analyse du cahier des charges, préparation des documents de base, recherche d'informations sur la puissance du moteur et des LEDs. | 5
Mardi | 08/08/2023 | 10 | Correction du planning, recherche d'informations et de composants pour la pré-étude, réunion d'une heure. | 3
Mercredi | 09/08/2023 | 9 | Recherche d'informations pour la pré-étude. | 4
Jeudi | 10/08/2023 | 9 | Recherche d'informations pour la pré-étude, début de la phase de conception avec le développement de la partie driver des LEDs. | 4
Vendredi | 11/08/2023 | 9 | Dimensionnement du driver des LEDs et de la communication avec l'appareil photo Nikon D750. | 3
Samedi | 12/08/2023
Dimanche | 13/08/2023 | 3 | Choix du LCD et du rétro-éclairage. | 2
Lundi | 14/08/2023 | 9 | Dimensionnement des systèmes de déclenchement d'appareils photo. | 5
Mardi | 15/08/2023 | 9 | Dimensionnement du driver de moteur et changement du driver de LED de puissance, choix du PIC et réunion de deux heures. | 4
Mercredi | 16/08/2023 | 9 | Dimensionnement du driver de moteur et du PIC32MK. | 4
Jeudi | 17/08/2023 | 8 | Correction de détails sur le schéma et conception du PCB. | 3
Vendredi | 18/08/2023 | 10 | Conception du PCB, revue du PCB par M. Zoubir et validation du PCB sur Eurocircuit. | 4
Samedi | 19/08/2023 | | | 3
Dimanche | 20/08/2023
Lundi | 21/08/2023 | 9 | Réalisation de la BOM, ajout des composants hors PCB, début du design mécanique. | 4
Mardi | 22/08/2023 | 8 | Commande des composants, conception mécanique du boîtier. | 4
Mercredi | 23/08/2023 | 9 | Finalisation de la conception du boîtier, réunion de 45 minutes. | 3
Jeudi | 24/08/2023 | 8 | Réception du PCB, montage du PIC32MK sur le PCB, début de programmation (génération de PWM). | 2
Vendredi | 25/08/2023 | 8 | Programmation pour test des PWMs, montage de composants sur le PCB. | 3
Samedi | 26/08/2023 | | | 3
Dimanche | 27/08/2023
Lundi | 28/08/2023 | 9 | Montage du PCB complet, programmation de test et installation du driver LCD. | 4
Mardi | 29/08/2023 | 9 | Programmation pour tester le LCD, les LED et le driver du moteur pas à pas. | 5
Mercredi | 30/08/2023 | 10 | Envoi du boîtier à imprimer, test des optocoupleurs, essai du contact Reed, programmation de l'affichage et des menus. | 4
Jeudi | 31/08/2023 | 10 | Programmation des menus et correction de bugs. | 5
Vendredi | 01/09/2023 | 9 | Programmation des menus et correction de bugs. | 5
Samedi | 02/09/2023
Dimanche | 03/09/2023 | 5 | Rattrapage du retard dans la rédaction du rapport. | 3
Lundi | 04/09/2023 | 10 | Rattrapage du retard dans la rédaction du rapport et programmation des menus. | 5
Mardi | 05/09/2023 | 10 | Programmation de la séquence et des menus de configuration. | 4
Mercredi | 06/09/2023 | 10 | Création d'un câble de commande d'appareil photo. | 3
Jeudi | 07/09/2023 | 10 | Test du déclenchement de l'appareil photo au palais de Rumine (musée), correction de bugs au niveau de la séquence des LEDs et programmation de la séquence complète. | 3
Vendredi | 08/09/2023 | 10 | Programmation des derniers points importants de la séquence. | 4
Samedi | 09/09/2023 | 8 | Mise en service et mesures des différents composants critiques du système. | 3
Dimanche | 10/09/2023 | 8 | Finalisation de la documentation et du rapport. | 3
Lundi | 11/09/2023 | 1 | Rendu du rapport.
Total | 253 | Total cafés : | 114

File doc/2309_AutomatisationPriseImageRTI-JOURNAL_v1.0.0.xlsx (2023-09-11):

Jour | Date | Nbr période | Tâches effectuées | Nbr de café
Lundi | 2023-08-07 | 7 | Réception et analyse du cahier des charges, préparation des documents de base, recherche d'informations sur la puissance du moteur et des LEDs. | 5
Mardi | 2023-08-08 | 10 | Correction du planning, recherche d'informations et de composants pour la pré-étude, réunion d'une heure. | 3
Mercredi | 2023-08-09 | 9 | Recherche d'informations pour la pré-étude. | 4
Jeudi | 2023-08-10 | 9 | Recherche d'informations pour la pré-étude, début de la phase de conception avec le développement de la partie driver des LEDs. | 4
Vendredi | 2023-08-11 | 9 | Dimensionnement du driver des LEDs et de la communication avec l'appareil photo Nikon D750. | 3
Samedi | 2023-08-12
Dimanche | 2023-08-13 | 3 | Choix du LCD et du rétro-éclairage. | 2
Lundi | 2023-08-14 | 9 | Dimensionnement des systèmes de déclenchement d'appareils photo. | 5
Mardi | 2023-08-15 | 9 | Dimensionnement du driver de moteur et changement du driver de LED de puissance, choix du PIC et réunion de deux heures. | 4
Mercredi | 2023-08-16 | 9 | Dimensionnement du driver de moteur et du PIC32MK. | 4
Jeudi | 2023-08-17 | 8 | Correction de détails sur le schéma et conception du PCB. | 3
Vendredi | 2023-08-18 | 10 | Conception du PCB, revue du PCB par M. Zoubir et validation du PCB sur Eurocircuit. | 4
Samedi | 2023-08-19 |  |  | 3
Dimanche | 2023-08-20
Lundi | 2023-08-21 | 9 | Réalisation de la BOM, ajout des composants hors PCB, début du design mécanique. | 4
Mardi | 2023-08-22 | 8 | Commande des composants, conception mécanique du boîtier. | 4
Mercredi | 2023-08-23 | 9 | Finalisation de la conception du boîtier, réunion de 45 minutes. | 3
Jeudi | 2023-08-24 | 8 | Réception du PCB, montage du PIC32MK sur le PCB, début de programmation (génération de PWM). | 2
Vendredi | 2023-08-25 | 8 | Programmation pour test des PWMs, montage de composants sur le PCB. | 3
Samedi | 2023-08-26 |  |  | 3
Dimanche | 2023-08-27
Lundi | 2023-08-28 | 9 | Montage du PCB complet, programmation de test et installation du driver LCD. | 4
Mardi | 2023-08-29 | 9 | Programmation pour tester le LCD, les LED et le driver du moteur pas à pas. | 5
Mercredi | 2023-08-30 | 10 | Envoi du boîtier à imprimer, test des optocoupleurs, essai du contact Reed, programmation de l'affichage et des menus. | 4
Jeudi | 2023-08-31 | 10 | Programmation des menus et correction de bugs. | 5
Vendredi | 2023-09-01 | 9 | Programmation des menus et correction de bugs. | 5
Samedi | 2023-09-02
Dimanche | 2023-09-03 | 5 | Rattrapage du retard dans la rédaction du rapport. | 3
Lundi | 2023-09-04 | 10 | Rattrapage du retard dans la rédaction du rapport et programmation des menus. | 5
Mardi | 2023-09-05 | 10 | Programmation de la séquence et des menus de configuration. | 4
Mercredi | 2023-09-06 | 10 | Création d'un câble de commande d'appareil photo. | 3
Jeudi | 2023-09-07 | 10 | Test du déclenchement de l'appareil photo au palais de Rumine (musée), correction de bugs au niveau de la séquence des LEDs et programmation de la séquence complète. | 3
Vendredi | 2023-09-08 | 10 | Programmation des derniers points importants de la séquence. | 4
Samedi | 2023-09-09 | 8 | Mise en service et mesures des différents composants critiques du système. | 3
Dimanche | 2023-09-10 | 8 | Finalisation de la documentation et du rapport. | 3
Lundi | 2023-09-11 | 1 | Rendu du rapport.
 | Total | 253 | Total cafés : | 114

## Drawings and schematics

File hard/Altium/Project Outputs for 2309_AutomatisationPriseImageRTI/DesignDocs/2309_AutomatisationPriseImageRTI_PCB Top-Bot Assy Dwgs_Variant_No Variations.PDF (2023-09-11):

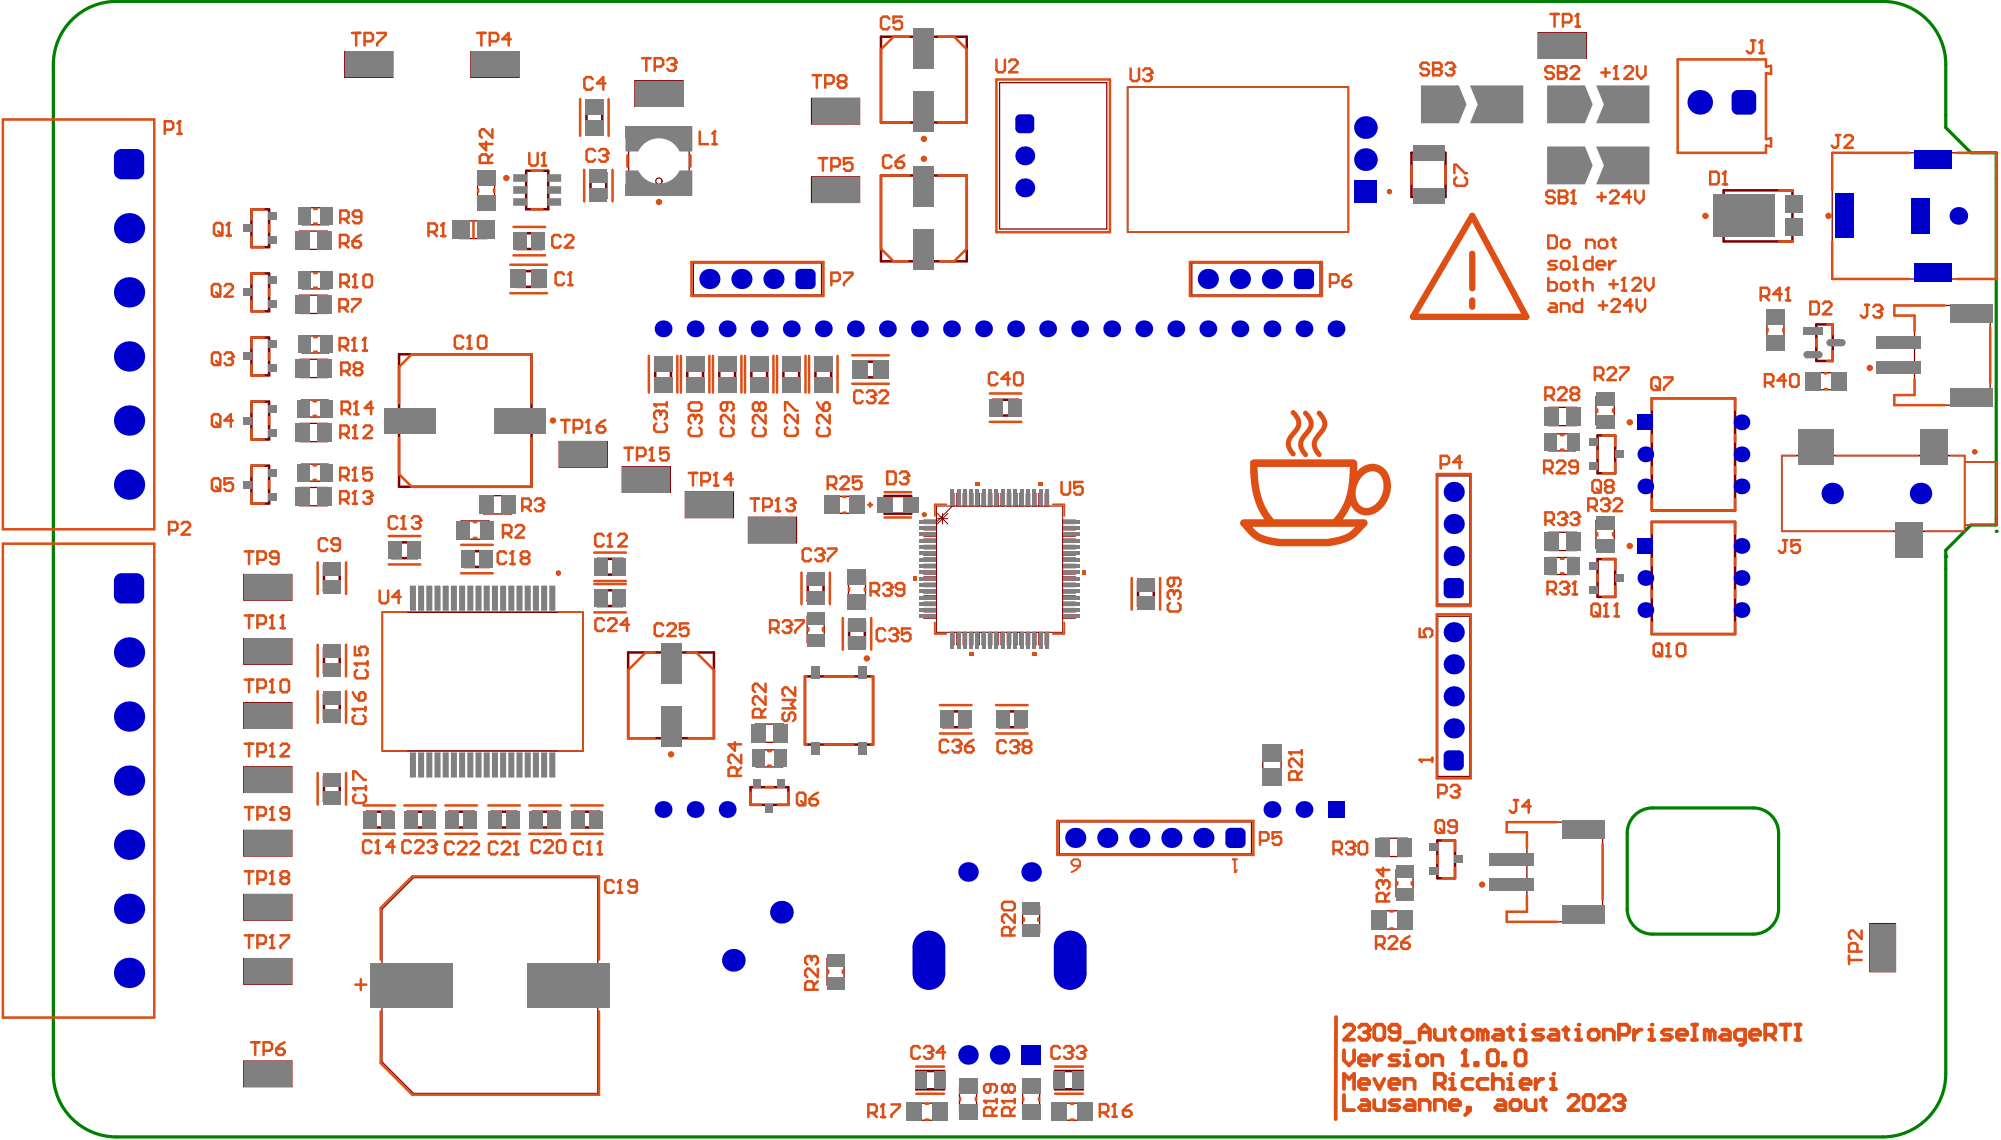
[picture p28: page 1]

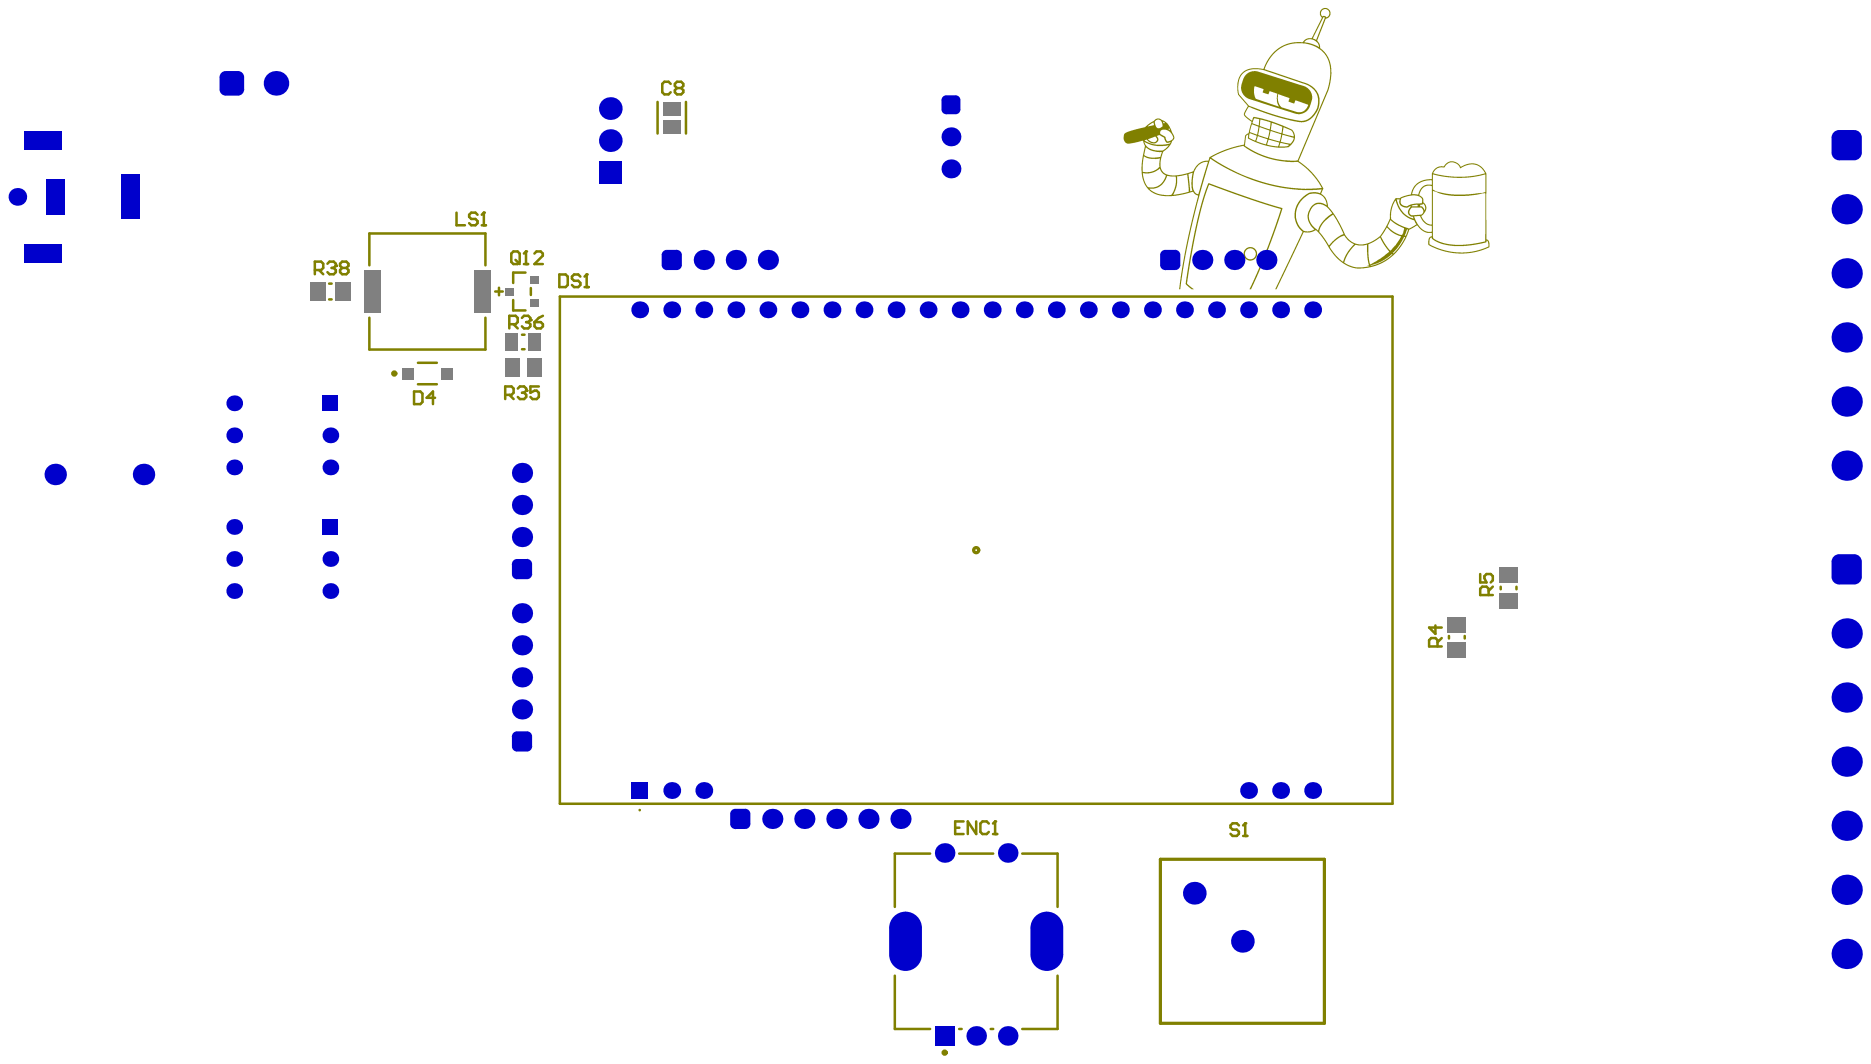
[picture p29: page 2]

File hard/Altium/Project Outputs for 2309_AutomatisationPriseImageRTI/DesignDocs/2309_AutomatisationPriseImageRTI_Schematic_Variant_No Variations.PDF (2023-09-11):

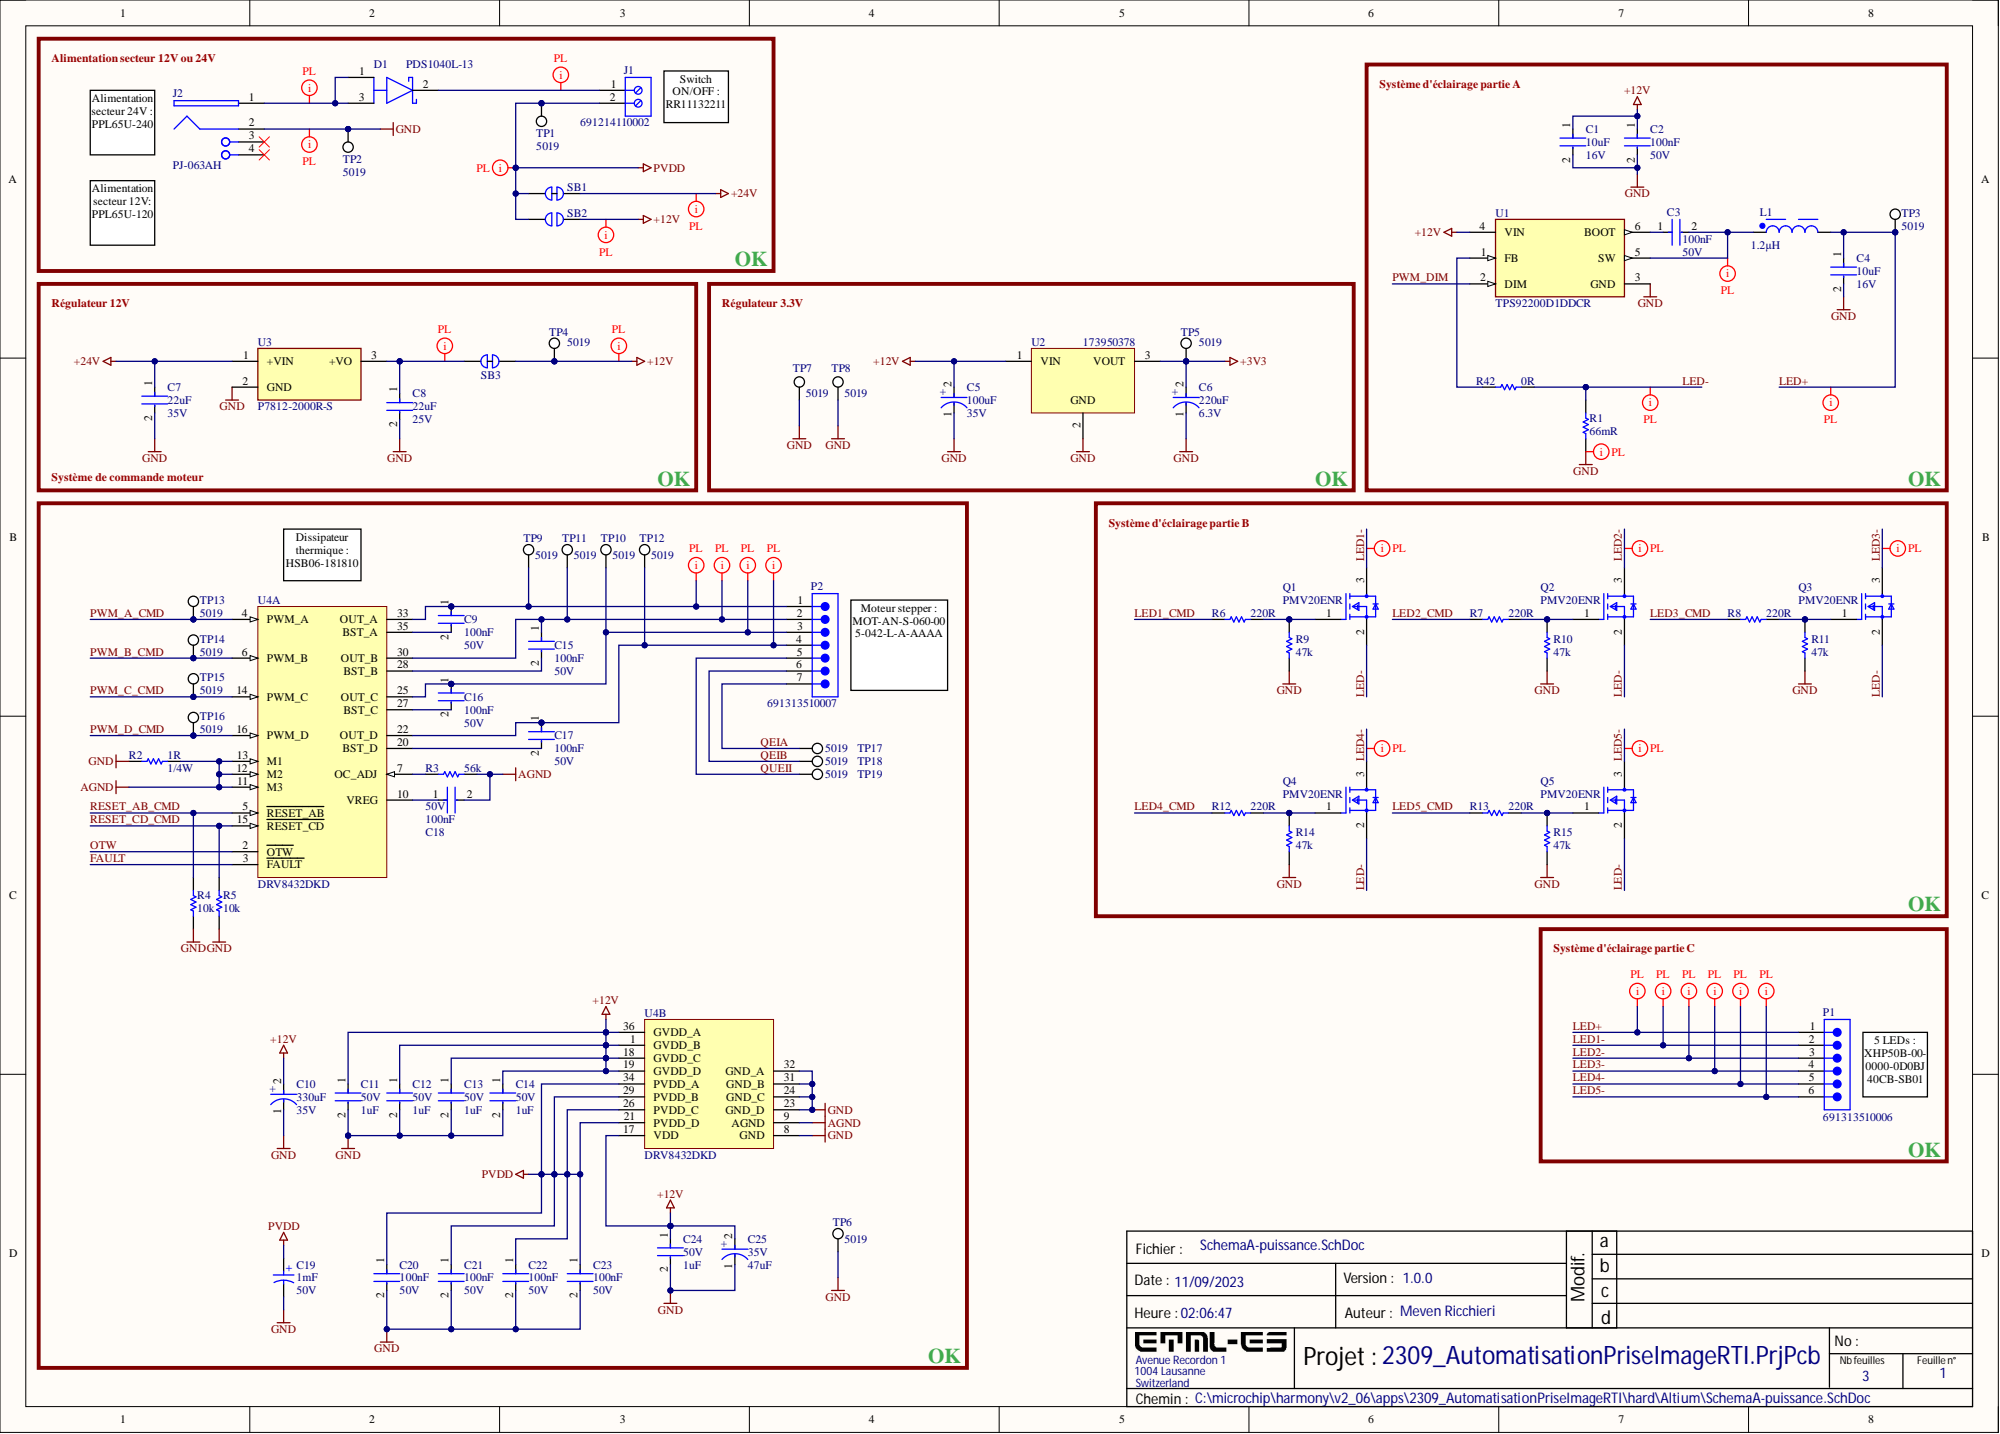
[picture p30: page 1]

50V | LED+ | 10uF

DIM 2

Système de commande moteur

U4B | | 691313510007 QEIA

RESET_CD_CMD | RESET_CD 15

OTW | | OTW 2
FAULT | | FAULT 3

SchemaA-puissance.SchDoc Fichier : | a

Date : 11/09/2023 | Version : 1.0.0

Heure : 02:06:47 | Meven Ricchieri Auteur :

Avenue Recordon 1
1004 Lausanne
Switzerland
Chemin : C:\microchip\harmony\v2_06\apps\2309_AutomatisationPriseImageRTI\hard\Altium\SchemaA-puissance.SchDoc

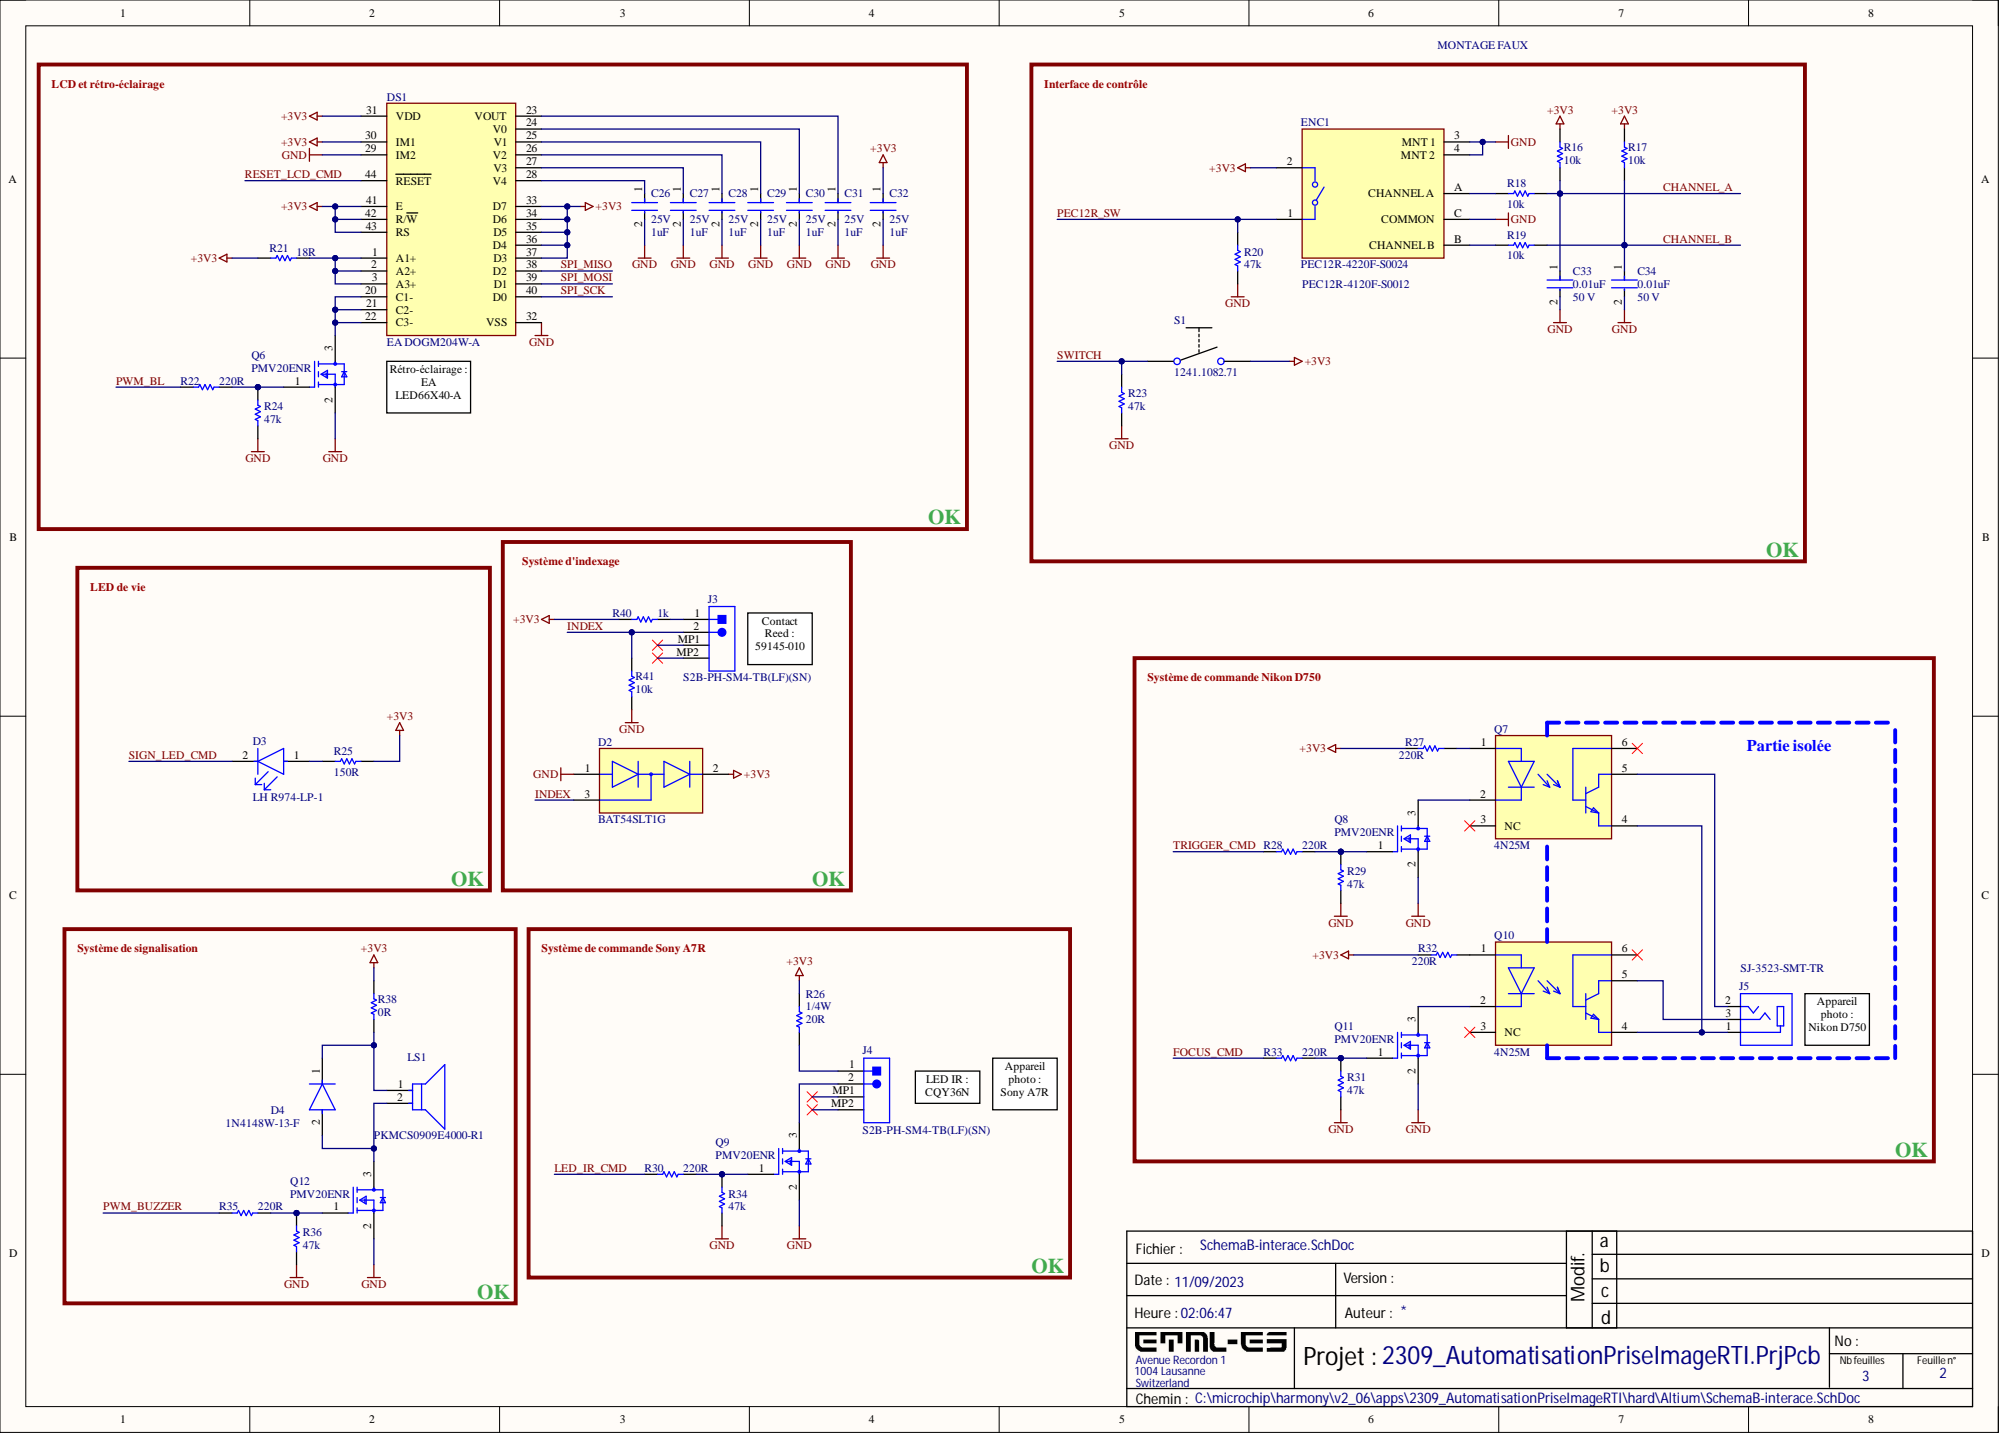
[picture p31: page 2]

LCD et rétro-éclairage

Système de commande Nikon D750

Système de commande Sony A7R

SchemaB-interace.SchDoc Fichier : | a

Date : 11/09/2023 | Version :

Avenue Recordon 1 1004 Lausanne Switzerland | Projet : 2309_AutomatisationPriseImageRTI.PrjPcb

Nb feuilles 3 | Feuille n° 2

Chemin : C:\microchip\harmony\v2_06\apps\2309_AutomatisationPriseImageRTI\hard\Altium\SchemaB-interace.SchDoc

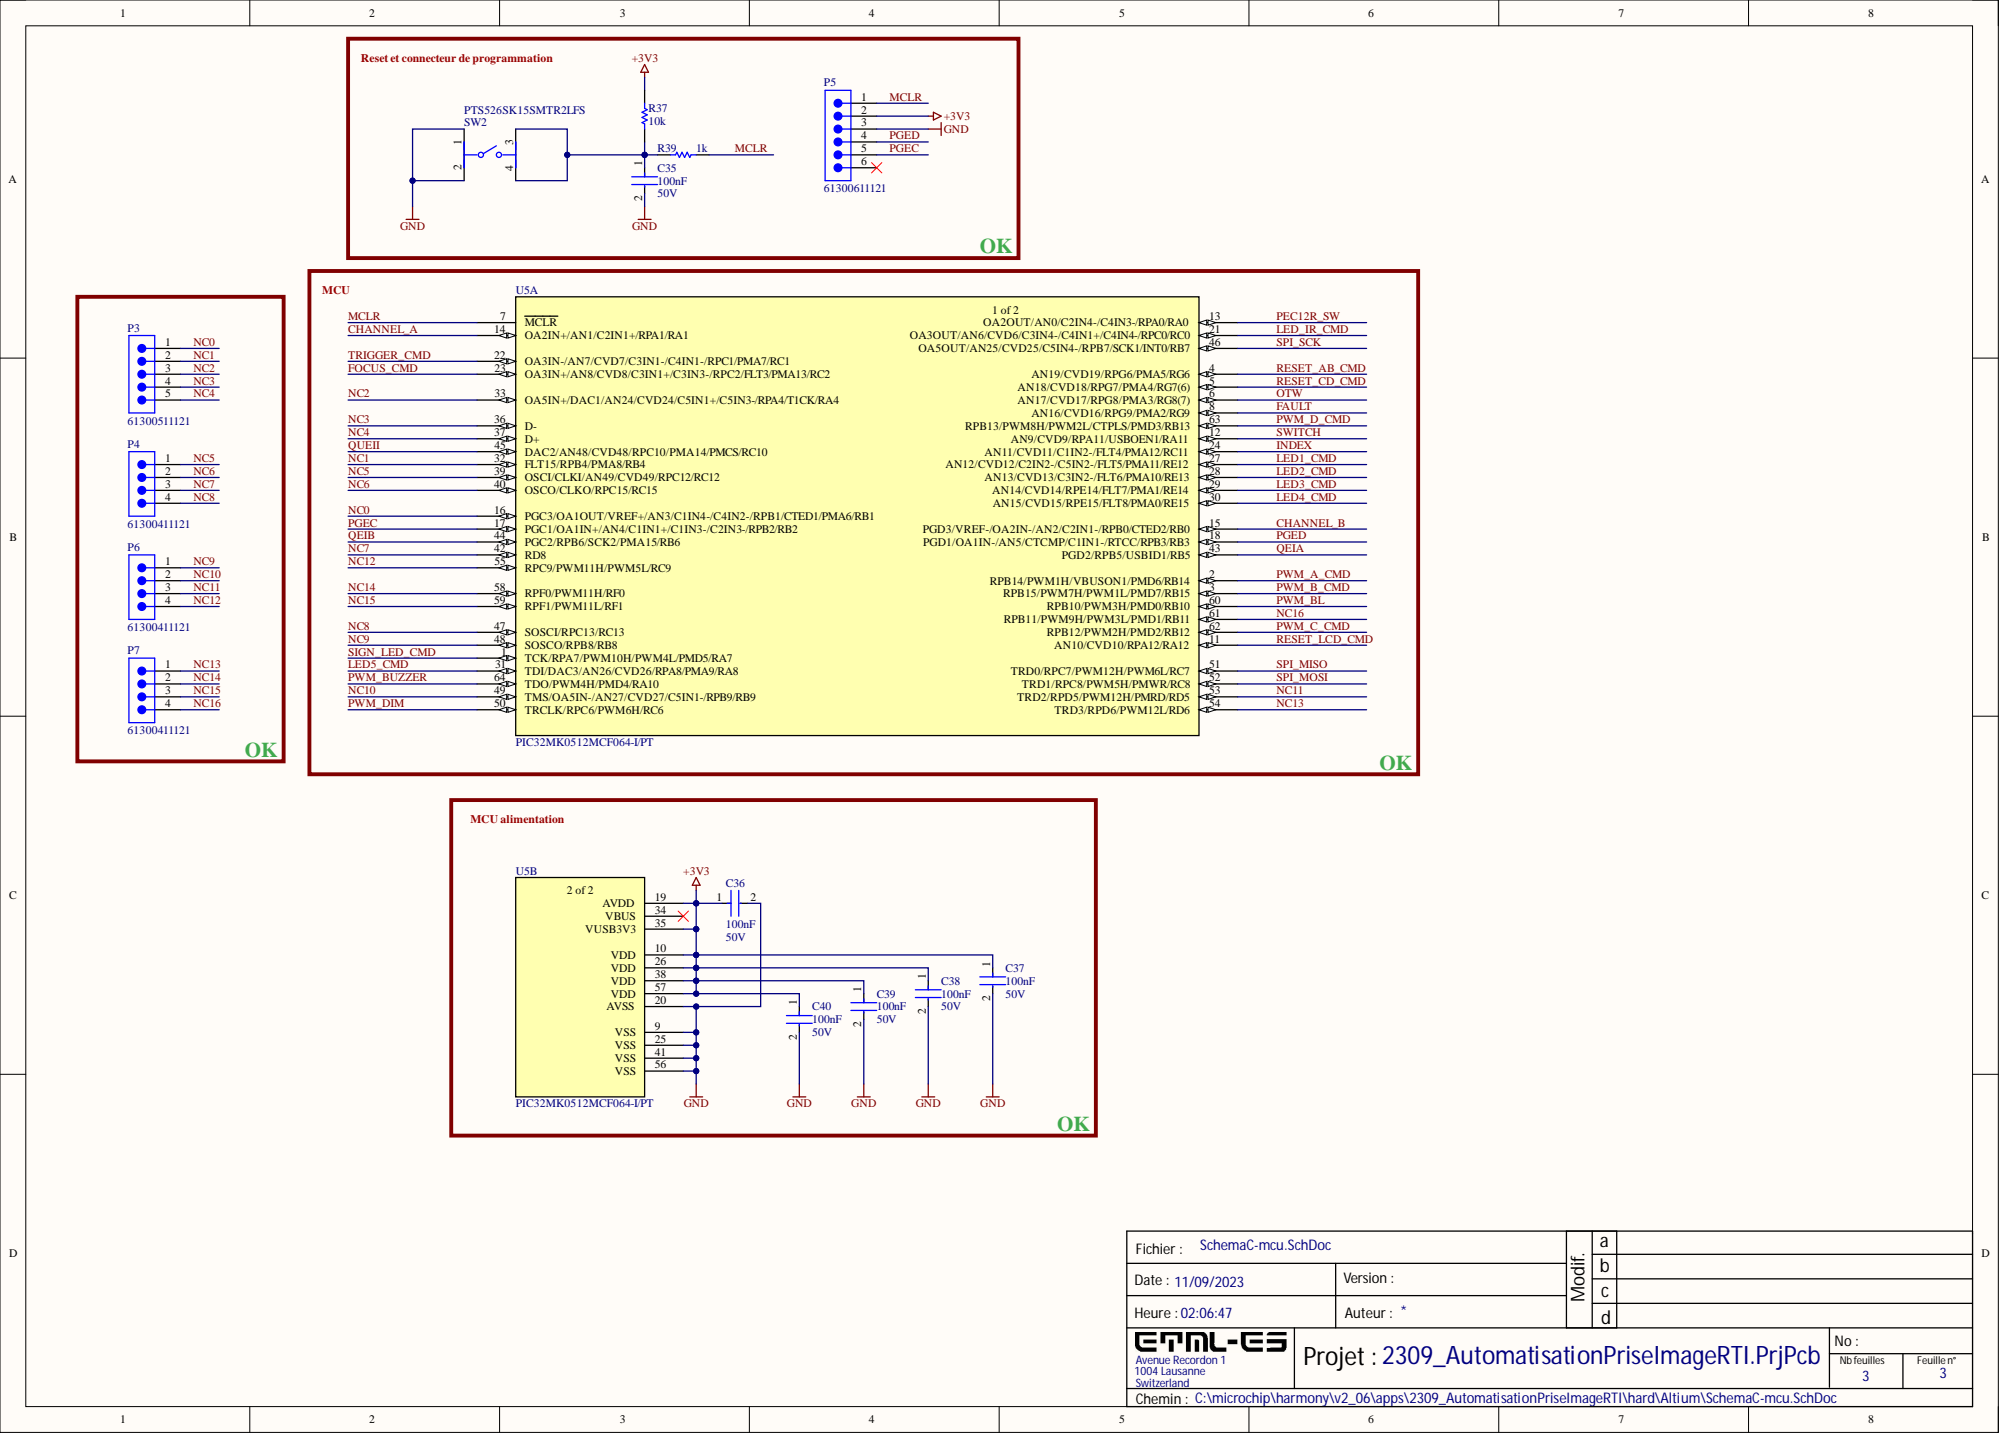
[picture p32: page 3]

Reset et connecteur de pro

2 6
3 8 | | D G | N
5 7 | | D G N
2 0 | | D G N

SchemaC-mcu. SchDoc Fichier :

Date : 11/09/2023 | Version :

Avenue Re cordon 1 004 Lausanne Switzerland | Projet : 2309_Automa tisa tionPriseImageRTI.PrjPcb

Nb feuille s | F euille n°

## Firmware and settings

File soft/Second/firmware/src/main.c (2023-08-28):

/*******************************************************************************
  Main Source File

  Company:
    Microchip Technology Inc.

  File Name:
    main.c

  Summary:
    This file contains the "main" function for a project.

  Description:
    This file contains the "main" function for a project.  The
    "main" function calls the "SYS_Initialize" function to initialize the state
    machines of all modules in the system
 *******************************************************************************/

// *****************************************************************************
// *****************************************************************************
// Section: Included Files
// *****************************************************************************
// *****************************************************************************

#include <stddef.h>                     // Defines NULL
#include <stdbool.h>                    // Defines true
#include <stdlib.h>                     // Defines EXIT_FAILURE
#include "definitions.h"                // SYS function prototypes


// *****************************************************************************
// *****************************************************************************
// Section: Main Entry Point
// *****************************************************************************
// *****************************************************************************

int main ( void )
{
    /* Initialize all modules */
    SYS_Initialize ( NULL );

        
        
    while ( true )
    {
        /* Maintain state machines of all polled MPLAB Harmony modules. */
        //SYS_Tasks ( );
        APP_Tasks();
        
    }

    /* Execution should not come here during normal operation */

    return ( EXIT_FAILURE );
}


/*******************************************************************************
 End of File
*/

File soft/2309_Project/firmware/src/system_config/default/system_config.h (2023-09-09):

/*******************************************************************************
  MPLAB Harmony System Configuration Header

  File Name:
    system_config.h

  Summary:
    Build-time configuration header for the system defined by this MPLAB Harmony
    project.

  Description:
    An MPLAB Project may have multiple configurations.  This file defines the
    build-time options for a single configuration.

  Remarks:
    This configuration header must not define any prototypes or data
    definitions (or include any files that do).  It only provides macro
    definitions for build-time configuration options that are not instantiated
    until used by another MPLAB Harmony module or application.

    Created with MPLAB Harmony Version 2.06
*******************************************************************************/

// DOM-IGNORE-BEGIN
/*******************************************************************************
Copyright (c) 2013-2015 released Microchip Technology Inc.  All rights reserved.

Microchip licenses to you the right to use, modify, copy and distribute
Software only when embedded on a Microchip microcontroller or digital signal
controller that is integrated into your product or third party product
(pursuant to the sublicense terms in the accompanying license agreement).

You should refer to the license agreement accompanying this Software for
additional information regarding your rights and obligations.

SOFTWARE AND DOCUMENTATION ARE PROVIDED AS IS WITHOUT WARRANTY OF ANY KIND,
EITHER EXPRESS OR IMPLIED, INCLUDING WITHOUT LIMITATION, ANY WARRANTY OF
MERCHANTABILITY, TITLE, NON-INFRINGEMENT AND FITNESS FOR A PARTICULAR PURPOSE.
IN NO EVENT SHALL MICROCHIP OR ITS LICENSORS BE LIABLE OR OBLIGATED UNDER
CONTRACT, NEGLIGENCE, STRICT LIABILITY, CONTRIBUTION, BREACH OF WARRANTY, OR
OTHER LEGAL EQUITABLE THEORY ANY DIRECT OR INDIRECT DAMAGES OR EXPENSES
INCLUDING BUT NOT LIMITED TO ANY INCIDENTAL, SPECIAL, INDIRECT, PUNITIVE OR
CONSEQUENTIAL DAMAGES, LOST PROFITS OR LOST DATA, COST OF PROCUREMENT OF
SUBSTITUTE GOODS, TECHNOLOGY, SERVICES, OR ANY CLAIMS BY THIRD PARTIES
(INCLUDING BUT NOT LIMITED TO ANY DEFENSE THEREOF), OR OTHER SIMILAR COSTS.
*******************************************************************************/
// DOM-IGNORE-END

#ifndef _SYSTEM_CONFIG_H
#define _SYSTEM_CONFIG_H

// *****************************************************************************
// *****************************************************************************
// Section: Included Files
// *****************************************************************************
// *****************************************************************************
/*  This section Includes other configuration headers necessary to completely
    define this configuration.
*/


// DOM-IGNORE-BEGIN
#ifdef __cplusplus  // Provide C++ Compatibility

extern "C" {

#endif
// DOM-IGNORE-END

// *****************************************************************************
// *****************************************************************************
// Section: System Service Configuration
// *****************************************************************************
// *****************************************************************************
// *****************************************************************************
/* Common System Service Configuration Options
*/
#define SYS_VERSION_STR           "2.06"
#define SYS_VERSION               20600

// *****************************************************************************
/* Clock System Service Configuration Options
*/
#define SYS_CLK_FREQ                        40000000ul
#define SYS_CLK_BUS_PERIPHERAL_1            40000000ul
#define SYS_CLK_BUS_PERIPHERAL_2            40000000ul
#define SYS_CLK_BUS_PERIPHERAL_3            40000000ul
#define SYS_CLK_BUS_PERIPHERAL_4            40000000ul
#define SYS_CLK_BUS_PERIPHERAL_5            40000000ul
#define SYS_CLK_BUS_PERIPHERAL_6            10000000ul
#define SYS_CLK_BUS_PERIPHERAL_7            40000000ul
#define SYS_CLK_CONFIG_PRIMARY_XTAL         24000000ul
#define SYS_CLK_CONFIG_SECONDARY_XTAL       32768ul
   
/*** Ports System Service Configuration ***/
#define SYS_PORT_A_ANSEL        0xE27C
#define SYS_PORT_A_TRIS         0xE67F
#define SYS_PORT_A_LAT          0x0000
#define SYS_PORT_A_ODC          0x0000
#define SYS_PORT_A_CNPU         0x1000
#define SYS_PORT_A_CNPD         0x0000
#define SYS_PORT_A_CNEN         0x0000

#define SYS_PORT_B_ANSEL        0x010E
#define SYS_PORT_B_TRIS         0xF7FF
#define SYS_PORT_B_LAT          0x0000
#define SYS_PORT_B_ODC          0x0000
#define SYS_PORT_B_CNPU         0x0000
#define SYS_PORT_B_CNPD         0x0000
#define SYS_PORT_B_CNEN         0x0000
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

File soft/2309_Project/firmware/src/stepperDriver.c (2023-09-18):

/* 
 * File:   stepperDriver.c
 * Author: ricch
 *
 * Created on August 30, 2023, 10:39 PM
 * 
 * DRV8432 driver 2H bridge
 */


#include <stepperDriver.h>

static STEPPER_DATA stepperData;
extern APP_DATA appData;


//----------------------------------------------------------------------------// initStepperData
void initStepperParam(void){
    
    stepperData.isAtHomeInCW     = false;
    stepperData.isAtHomeInCCW    = false;
//    stepperData.isIndexed        = false;
    stepperData.isInAutoHomeSeq  = false;
    
    stepperData.performedSteps   = 0; 
    stepperData.stepToReach      = 0; 
    
    stepperData.stepPerSec       = 50; /* speed */
    
    stepperData.stepPerTurn      = 200; /* Data from igus 
                                         * MOT-AN-S-060-005-042-L-A-AAAA */
    stepperData.anglePerStep     = 1.8; /* " */
    
    stepperData.gearValue        = 1; /* 260 -> Data from meca student */
    
    stepperData.dutyCycleStepper = 10; /* Min 0 - max 199 */ 
}

void initStepperMotor(){
    
    changeSpeed(getMyStepperStruct());
    setStepperPower(getMyStepperStruct(), &stepperData.dutyCycleStepper); // -< param ??!! faux
    /* Disable RESET on both H bridge */
    RESET_AB_CMDOn();
    RESET_CD_CMDOn();
}

//----------------------------------------------------------------------------// turnOffStepperPwms
/* Disable all PWMs for motor control */
void turnOffStepperPwms(void){
    
    /* A */
    PLIB_MCPWM_ChannelPWMxHDisable (MCPWM_ID_0 ,MCPWM_CHANNEL1);
    /* B */
    PLIB_MCPWM_ChannelPWMxHDisable (MCPWM_ID_0 ,MCPWM_CHANNEL2);
    /* A_ */
    PLIB_MCPWM_ChannelPWMxLDisable (MCPWM_ID_0 ,MCPWM_CHANNEL1);
    /* B_ */
    PLIB_MCPWM_ChannelPWMxLDisable (MCPWM_ID_0 ,MCPWM_CHANNEL2);
}

//----------------------------------------------------------------------------// changeSpeed
void changeSpeed(STEPPER_DATA *pStepperData){
    
    uint16_t tmr2Id3Perdiod = 0;
    uint16_t frequency = 0;
    
    frequency = pStepperData->stepPerSec;
    tmr2Id3Perdiod = SYS_CLK / (frequency * 16) - 1; /* PRESCALER = 16 */
    PLIB_TMR_Counter16BitClear(TMR_ID_3);
    PLIB_TMR_Period16BitSet(TMR_ID_3, tmr2Id3Perdiod);
}

//----------------------------------------------------------------------------// processStepper
void processStepper(STEPPER_DATA *pStepperData){
    
    static uint8_t step = 0;
    //---------------------------// Counter clockwise CCW
    if(pStepperData->performedSteps > pStepperData->stepToReach){
        if(pStepperData->isAtHomeInCCW == false){
            switch(step){
                /* Sequence of 4 steps for CCW rotation */
                case 1:
                    /* A */
                    PLIB_MCPWM_ChannelPWMxHEnable (MCPWM_ID_0 ,MCPWM_CHANNEL1);
                    /* B */
                    PLIB_MCPWM_ChannelPWMxHDisable(MCPWM_ID_0 ,MCPWM_CHANNEL2);
                    /* A_ */
                    PLIB_MCPWM_ChannelPWMxLDisable(MCPWM_ID_0 ,MCPWM_CHANNEL1);
                    /* B_ */
                    PLIB_MCPWM_ChannelPWMxLEnable (MCPWM_ID_0 ,MCPWM_CHANNEL2);
                    break;

                case 2:
                    PLIB_MCPWM_ChannelPWMxHEnable (MCPWM_ID_0 ,MCPWM_CHANNEL1);
                    PLIB_MCPWM_ChannelPWMxHEnable (MCPWM_ID_0 ,MCPWM_CHANNEL2);
                    PLIB_MCPWM_ChannelPWMxLDisable(MCPWM_ID_0 ,MCPWM_CHANNEL1);
                    PLIB_MCPWM_ChannelPWMxLDisable(MCPWM_ID_0 ,MCPWM_CHANNEL2);
                    break;

                case 3:
                    PLIB_MCPWM_ChannelPWMxHDisable(MCPWM_ID_0 ,MCPWM_CHANNEL1);
                    PLIB_MCPWM_ChannelPWMxHEnable (MCPWM_ID_0 ,MCPWM_CHANNEL2);
                    PLIB_MCPWM_ChannelPWMxLEnable (MCPWM_ID_0 ,MCPWM_CHANNEL1);
                    PLIB_MCPWM_ChannelPWMxLDisable(MCPWM_ID_0 ,MCPWM_CHANNEL2);
                    break;

                case 0:
                    PLIB_MCPWM_ChannelPWMxHDisable(MCPWM_ID_0 ,MCPWM_CHANNEL1);
                    PLIB_MCPWM_ChannelPWMxHDisable(MCPWM_ID_0 ,MCPWM_CHANNEL2);
                    PLIB_MCPWM_ChannelPWMxLEnable (MCPWM_ID_0 ,MCPWM_CHANNEL1);
                    PLIB_MCPWM_ChannelPWMxLEnable (MCPWM_ID_0 ,MCPWM_CHANNEL2);
                    break;
            }
            step++;
        }
        /* Four steps performed in CCW */
        if(step == 4){
            
            step = 0;
            pStepperData->performedSteps -= 4;
        }
    }
        
    /* Index is reach in CCW */
    if(INDEXStateGet() && pStepperData->isAtHomeInCW == false){

        pStepperData->isAtHomeInCCW = true;

        if(pStepperData->isInAutoHomeSeq == true){

            /* Set the values to zero */
            pStepperData->stepToReach = 0;
            pStepperData->performedSteps = 0;
            /* Reset the flag isInAutoHomeSeq */
            pStepperData->isInAutoHomeSeq = false;

            appData.indexState = IS_DONE;
        }
    } else {
        pStepperData->isAtHomeInCCW = false;
    }    
    
    
    
    //---------------------------// Clockwise CW
    if(pStepperData->performedSteps < pStepperData->stepToReach){
        if(pStepperData->isAtHomeInCW == false){
            switch(step){
                /* Sequence of 4 steps for CW rotation */
                case 1:
                    /* A */
                    PLIB_MCPWM_ChannelPWMxHEnable (MCPWM_ID_0 ,MCPWM_CHANNEL1);
                    /* B */
                    PLIB_MCPWM_ChannelPWMxHDisable(MCPWM_ID_0 ,MCPWM_CHANNEL2);
                    /* A_ */
                    PLIB_MCPWM_ChannelPWMxLDisable(MCPWM_ID_0 ,MCPWM_CHANNEL1);
                    /* B_ */
                    PLIB_MCPWM_ChannelPWMxLEnable (MCPWM_ID_0 ,MCPWM_CHANNEL2);
                    break;

                case 0:
                    PLIB_MCPWM_ChannelPWMxHEnable (MCPWM_ID_0 ,MCPWM_CHANNEL1);
                    PLIB_MCPWM_ChannelPWMxHEnable (MCPWM_ID_0 ,MCPWM_CHANNEL2);
                    PLIB_MCPWM_ChannelPWMxLDisable(MCPWM_ID_0 ,MCPWM_CHANNEL1);
                    PLIB_MCPWM_ChannelPWMxLDisable(MCPWM_ID_0 ,MCPWM_CHANNEL2);
                    break;

                case 3:
                    PLIB_MCPWM_ChannelPWMxHDisable(MCPWM_ID_0 ,MCPWM_CHANNEL1);
                    PLIB_MCPWM_ChannelPWMxHEnable (MCPWM_ID_0 ,MCPWM_CHANNEL2);
                    PLIB_MCPWM_ChannelPWMxLEnable (MCPWM_ID_0 ,MCPWM_CHANNEL1);
                    PLIB_MCPWM_ChannelPWMxLDisable(MCPWM_ID_0 ,MCPWM_CHANNEL2);
                    break;
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

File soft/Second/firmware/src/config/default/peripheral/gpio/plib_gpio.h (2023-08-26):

/*******************************************************************************
  GPIO PLIB

  Company:
    Microchip Technology Inc.

  File Name:
    plib_gpio.h UUUUUUUUU

  Summary:
    GPIO PLIB Header File

  Description:
    This library provides an interface to control and interact with Parallel
    Input/Output controller (GPIO) module.

*******************************************************************************/

/*******************************************************************************
* Copyright (C) 2019 Microchip Technology Inc. and its subsidiaries.
*
* Subject to your compliance with these terms, you may use Microchip software
* and any derivatives exclusively with Microchip products. It is your
* responsibility to comply with third party license terms applicable to your
* use of third party software (including open source software) that may
* accompany Microchip software.
*
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
* IN NO EVENT WILL MICROCHIP BE LIABLE FOR ANY INDIRECT, SPECIAL, PUNITIVE,
* INCIDENTAL OR CONSEQUENTIAL LOSS, DAMAGE, COST OR EXPENSE OF ANY KIND
* WHATSOEVER RELATED TO THE SOFTWARE, HOWEVER CAUSED, EVEN IF MICROCHIP HAS
* BEEN ADVISED OF THE POSSIBILITY OR THE DAMAGES ARE FORESEEABLE. TO THE
* FULLEST EXTENT ALLOWED BY LAW, MICROCHIP'S TOTAL LIABILITY ON ALL CLAIMS IN
* ANY WAY RELATED TO THIS SOFTWARE WILL NOT EXCEED THE AMOUNT OF FEES, IF ANY,
* THAT YOU HAVE PAID DIRECTLY TO MICROCHIP FOR THIS SOFTWARE.
*******************************************************************************/

#ifndef PLIB_GPIO_H
#define PLIB_GPIO_H

#include <device.h>
#include <stdint.h>
#include <stdbool.h>
#include <stddef.h>

// DOM-IGNORE-BEGIN
#ifdef __cplusplus  // Provide C++ Compatibility

    extern "C" {

#endif
// DOM-IGNORE-END

// *****************************************************************************
// *****************************************************************************
// Section: Data types and constants
// *****************************************************************************
// *****************************************************************************


/*** Macros for SIGN_LED_CMD pin ***/
#define SIGN_LED_CMD_Set()               (LATASET = (1U<<7))
#define SIGN_LED_CMD_Clear()             (LATACLR = (1U<<7))
#define SIGN_LED_CMD_Toggle()            (LATAINV= (1U<<7))
#define SIGN_LED_CMD_OutputEnable()      (TRISACLR = (1U<<7))
#define SIGN_LED_CMD_InputEnable()       (TRISASET = (1U<<7))
#define SIGN_LED_CMD_Get()               ((PORTA >> 7) & 0x1U)
#define SIGN_LED_CMD_PIN                  GPIO_PIN_RA7

/*** Macros for PWM_A_CMD pin ***/
#define PWM_A_CMD_Get()               ((PORTB >> 14) & 0x1U)
#define PWM_A_CMD_PIN                  GPIO_PIN_RB14


// *****************************************************************************
/* GPIO Port

  Summary:
    Identifies the available GPIO Ports.

  Description:
    This enumeration identifies the available GPIO Ports.

  Remarks:
    The caller should not rely on the specific numbers assigned to any of
    these values as they may change from one processor to the next.

    Not all ports are available on all devices.  Refer to the specific
    device data sheet to determine which ports are supported.
*/


#define    GPIO_PORT_A  (0)
#define    GPIO_PORT_B  (1)
#define    GPIO_PORT_C  (2)
#define    GPIO_PORT_D  (3)
#define    GPIO_PORT_E  (4)
#define    GPIO_PORT_F  (5)
#define    GPIO_PORT_G  (6)
typedef uint32_t GPIO_PORT;

typedef enum
{
    GPIO_INTERRUPT_ON_MISMATCH,
    GPIO_INTERRUPT_ON_RISING_EDGE,
    GPIO_INTERRUPT_ON_FALLING_EDGE,
    GPIO_INTERRUPT_ON_BOTH_EDGES,
}GPIO_INTERRUPT_STYLE;

// *****************************************************************************
/* GPIO Port Pins

  Summary:
    Identifies the available GPIO port pins.

  Description:
    This enumeration identifies the available GPIO port pins.

  Remarks:
    The caller should not rely on the specific numbers assigned to any of
    these values as they may change from one processor to the next.

    Not all pins are available on all devices.  Refer to the specific
    device data sheet to determine which pins are supported.
*/
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

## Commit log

2023-08-07 First doc
    [2309_AutomatisationPriseImageRTI-JOURNAL_v1.0.0.xlsx, 2309_AutomatisationPriseImageRTI-PLANNING_v1.0.0.xlsx]
2023-08-07 Doc updated
    [2309_AutomatisationPriseImageRTI-JOURNAL_v1.0.0.xlsx, 2309_AutomatisationPriseImageRTI-PLANNING_v1.0.0.xlsx]
2023-08-07 Journal et planning mis à jour
    [2309_AutomatisationPriseImageRTI-JOURNAL_v1.0.0.xlsx, 2309_AutomatisationPriseImageRTI-PLANNING_v1.0.0.xlsx]
2023-08-08 Journal et planning updated
    [2309_AutomatisationPriseImageRTI-JOURNAL_v1.0.0.xlsx, 2309_AutomatisationPriseImageRTI-PLANNING_v1.0.0.xlsx]
2023-08-10 Altium Files
    [2309_AutomatisationPriseImageRTI.PrjPcb, PCB.PcbDoc, Schema.SchDoc]
2023-08-10 Journal updated
    [2309_AutomatisationPriseImageRTI-JOURNAL_v1.0.0.xlsx]
2023-08-12 Altium files updated
    [FootprintsLib.PcbLib, Schema.SchDoc, SymbLib.SchLib]
2023-08-14 New schematic file
    [Schema.SchDoc, SchemaA.SchDoc, SchemaB.SchDoc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]
2023-08-16 End of day
    [2309_AutomatisationPriseImageRTI.PrjPcb, CONV_RCD-24-0.70.PcbLib, FootprintsLib.PcbLib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]
2023-08-17 Altium PCB design
    [FootprintsLib.PcbLib, SchemaA-puissance.SchDoc, SchemaB-interace.SchDoc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]
2023-08-18 PCB finshed
    [2309_AutomatisationPriseImageRTI.PrjPcb, FootprintsLib.PcbLib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]
2023-08-18 Version corrigée
    [1815C.PcbDoc, 2309_AutomatisationPriseImageRTI.PrjPcb, ES_PCB_6C_2L_2023.PcbDoc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]
2023-08-24 Soft started
    [2309_AutomatisationPriseImageRTI_BOM1.xlsx]
2023-08-25 Softs for PWM
    [SchemaA-puissance.SchDoc, SchemaB-interace.SchDoc, SchemaC-mcu.SchDoc]
2023-08-28 PCB monté
    [2309_AutomatisationPriseImageRTI-JOURNAL_v1.0.0.xlsx]
2023-08-29 Stepper motor driver 50%, LED dimmer 50% and LCD OK
2023-08-30 Stepper motor OK
    [2309_AutomatisationPriseImageRTI-JOURNAL_v1.0.0.xlsx, 2309_AutomatisationPriseImageRTI-PLANNING_v1.0.0.xlsx, PartieBasse.step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]
2023-08-31 PWM for stepper motor fixed at 75%
    [2309_AutomatisationPriseImageRTI-JOURNAL_v1.0.0.xlsx, 2309_AutomatisationPriseImageRTI-PLANNING_v1.0.0.xlsx]
2023-09-04 Backlight management good
    [2309_AutomatisationPriseImageRTI-JOURNAL_v1.0.0.xlsx, 2309_AutomatisationPriseImageRTI-PLANNING_v1.0.0.xlsx]
